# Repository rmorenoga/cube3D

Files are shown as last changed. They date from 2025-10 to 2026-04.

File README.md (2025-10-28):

https://github.com/user-attachments/assets/da8bfa61-0a1e-48aa-958f-0410e7f2b091

# Smart Cellular Bricks for Decentralized Shape Classification and Damage Recovery

## System Requirements
### Hardware requirements
Training, simulation and plot generation are setup as a Python jupyter notebook **BIGCUBE_V2.ipynb**. We reccomend Google [colab](https://colab.research.google.com/) to run it. To open the notebook in colab you can either clone this repository and upload the notebook to Google colab, or create a fork of the repository and open it directly from github using Google colab. Most cells run on the free version of colab, however, for training you should use one of the paid plans as it uses resources over the free limits (12 GB of RAM).

Firmware compilation and communication with the cubes has been tested on a standard computer running Windows 10 or 11. See **Cube Firmware** below. 

The electronics folder contains the electronic designs necessary to build a cube in order to run the classification code in the robots. 

### Software requirements
Follow the instructions in the jupyter notebook to install the required Python packages and run the different cells. The notebook runs on the 2025.07 runtime version of colab (see more information [here](https://research.google.com/colaboratory/runtime-version-faq.html#2025.07)). Other Python packages required include (See **Install all required python packages** inside the notebook):
- keras==2.11.0
- tensorflow==2.12.0
- pygifsicle

and the **gifsicle** program which can be installed by calling in a cell:

	!sudo apt-get install gifsicle

Uploading the firmware to the cubes uses Python scripts, the requirements.txt in /OTAPython/ lists the necessary dependencies.
Getting data from the cubes requires installing [docker](docker.com/) in your system.

Both functions have been tested in a standard computer with Windows 11. See further details in each section below.

# Installation instructions 

Training and simulation are performed using python code organized in a jupyter notebook that runs preferably in Google colab **BIGCUBE_V2.ipynb**. To open it you can either clone this repository and upload the notebook to Google colab, or create a fork of the repository and open it directly from github using Google colab. The notebook also contains functions for exporting the model weights as a file for compiling the microcontroller code, tools for checking connections between real cubes and tools for generating graphs. For further instructions check the different cell descriptions inside the notebook. 

## Outputting neural network for firmware
To output the neural network to be uploaded to the firmware, run the corresponding cell in the jupyter notebook. It produces a text file that can be copied directly into the neural_network.h required by the firmware.

## Cube firmware
The cube firmware is saved in the 3DCubePlatformIO folder. You also need the neural_network.h file located in the root file of the repository. The following steps have been tested on Windows 10 and 11.

### Compiling
To be able to upload the firmware to the cubes it should first be compiled. The 3DCubePlatformIO folder is set up and configured as a [platformIO](platformio.org/) project. To make things easier we reccomend opening the folder with [visual studio code](https://code.visualstudio.com/). VSCode will automatically detect the platformio.ini file in the repository and ask you to install the platformIO extension. The extension will then automatically donwload all the required compilers and libraries. After installation press the compile button (check mark at the bottom left corner of VSCode). This will generate the firmware.bin file in the 3DCubePlatformIO/.pio/build/adafruit_metro_esp32s2/ subfolder. 

### Uploading
To upload the firmware.bin file first make sure the cubes are connected to the same local network. Then navigate to the OTApython folder and run the ESPuploadParallel.py script. This script should upload the firmware to all cubes connected in the network. To change the subnet that is scanned by the script, change the address ranges in lines 18, 80, 86, 52 and 53.

### Getting data from the cubes

After all cubes have been programmed. Turn them off, navigate to the StateReceivers folder in a terminal and launch the following command:

	docker compose up

 This will run the server configured in **docker-compose.yaml**. This requires that you have [docker](docker.com/) installed in your system and assumes that you have a [mongodb](mongodb.com/) installation with a **Test** database and a **Dummy** collection set up. Additionally make sure that the computer where you launch the server is on IP 192.168.72.22 and that you have firewall permissions to receive on TCP port 8000. You can change the server address in the firmware (/3DCubePlatformIO/src/3d_cube.ino) in line 688, this needs the cubes to be reprogrammed. After you launch the server, turn on the assembled cubes. The cubes will first perform the classification process, then connect to the network specified in lines 602 and 603 in the firmware (/3DCubePlatformIO/src/3d_cube.ino) and then post the data to the server.

After the data from all cubes arrive to the server, you can export the collection as a .json file.

## Electronics
This folder contains the electronic PCB designs necessary to fabricate a cube.

## Training Data:

The training data is downloaded from https://www.shapenet.org/ as ModelShapeNetCore, model_normalized.solid.binvox format. We use 7 classes: aircraft, boat, car, guitar, birdhouse(house), table and chair.

This data is then reduced by the function “training_data_cleaning.py”. Running this file will present you with scaled down versions of the downloaded training data. If you think the image is acceptable, close the image popup, and write “y” into the terminal. Else, write “n” in the terminal. The terminal will display how many successful images have been saved and also the number of voxels in each piece of data. Note: the data is expected to be in the file subfolder location vox_data/…. Cleaning the data is done one class at a time, and labels are saved simultaneously with the xdata. To change the class type, change line 129. 

The classification output should be as follows:

**N.  Class   Color**
- 0 **Plane** green  
- 1 **Chair** blue  
- 2 **Car** purple  
- 3 **Table** yellow 
- 4 **House** white  
- 5 **Guitar** pink  
- 6 **Boat** cyan
- **Damaged** red

The code will output two .npy files xdata and ydata that are ready to be inputted to the neural network training code. **Already cleaned data is stored in the xdata_7class.npy and ydata_7class.npy**

## Training for damage detection and recovery

Our code for damage detection and recovery can be found here: https://github.com/shyamsn97/cube-regen

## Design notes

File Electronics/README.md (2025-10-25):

# Electronic PCB design files

This folder contains the design files for fabricating the PCBs that make the sides of the cube and that enable processing, power and communication. Each folder contains a [Kicad](kicad.org/) project with both schematics and layout files. 

## 3DESPWrover 
This is the top PCB that contains an ESP32-WROOVER module, a DC-DC step down converter and a Neo-pixel RGB led. The BoardTest subfolder contains test code to check that all components are working properly in the board. This PCB contains a 14-way micromatch connector to connect this and the bottom PCB together. One top PCB is required for one cube.

## 3DESPWroverS
This is the side PCB. This PCB contains only communication and power headers as well as soldering connections to attach it to other similar PCBs and the bottom one. Four identical side PCBs are required for one cube.

## 3DESPWroverB
This is the bottom PCB. This PCB contains only communication and power headers as well as soldering connections to attach it to the side PCBs. This PCB contains a 14-way micromatch connector to connect this and the top PCB together. One bottom PCB is required for one cube.

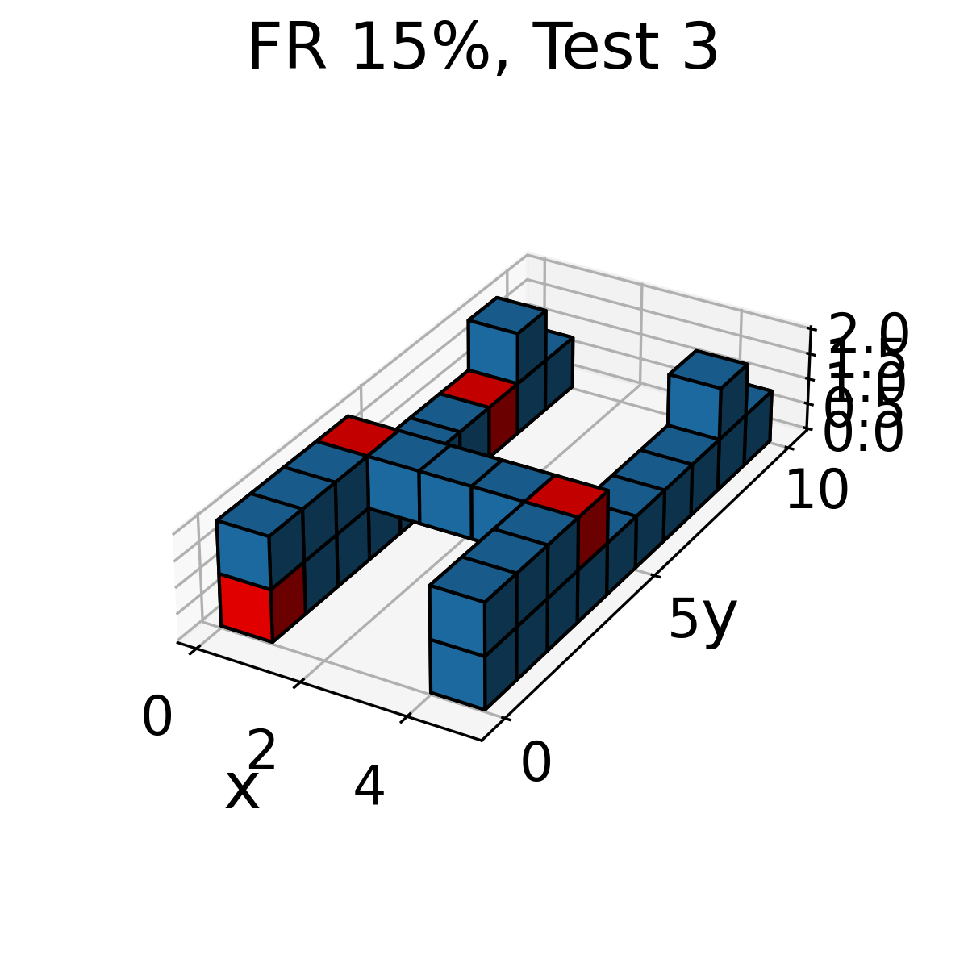
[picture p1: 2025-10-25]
Experiment data/hardware/Boat_144/Boat_144_FR15_T3.png

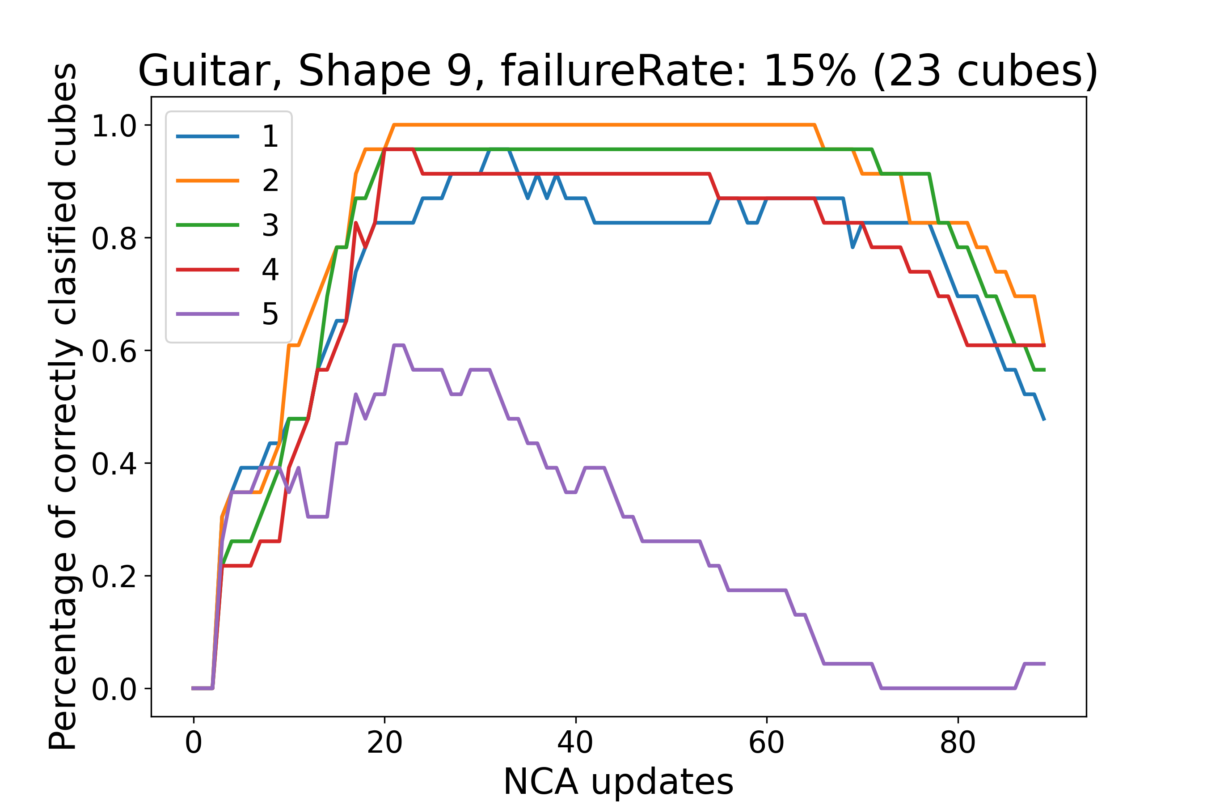
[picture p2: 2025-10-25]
Experiment data/hardware/Guitar_9/GraphGuitar_9_FR15.png

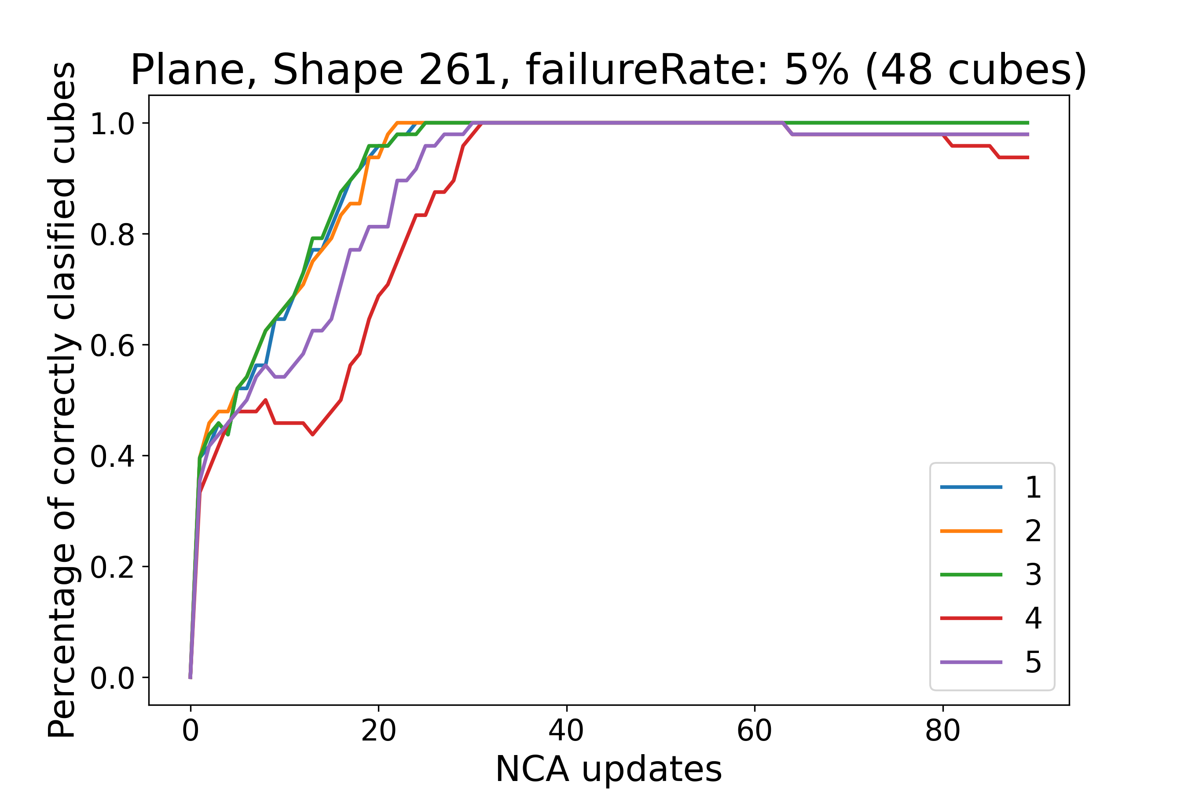
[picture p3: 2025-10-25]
Experiment data/hardware/Plane_261/GraphPlane_261_FR5.png

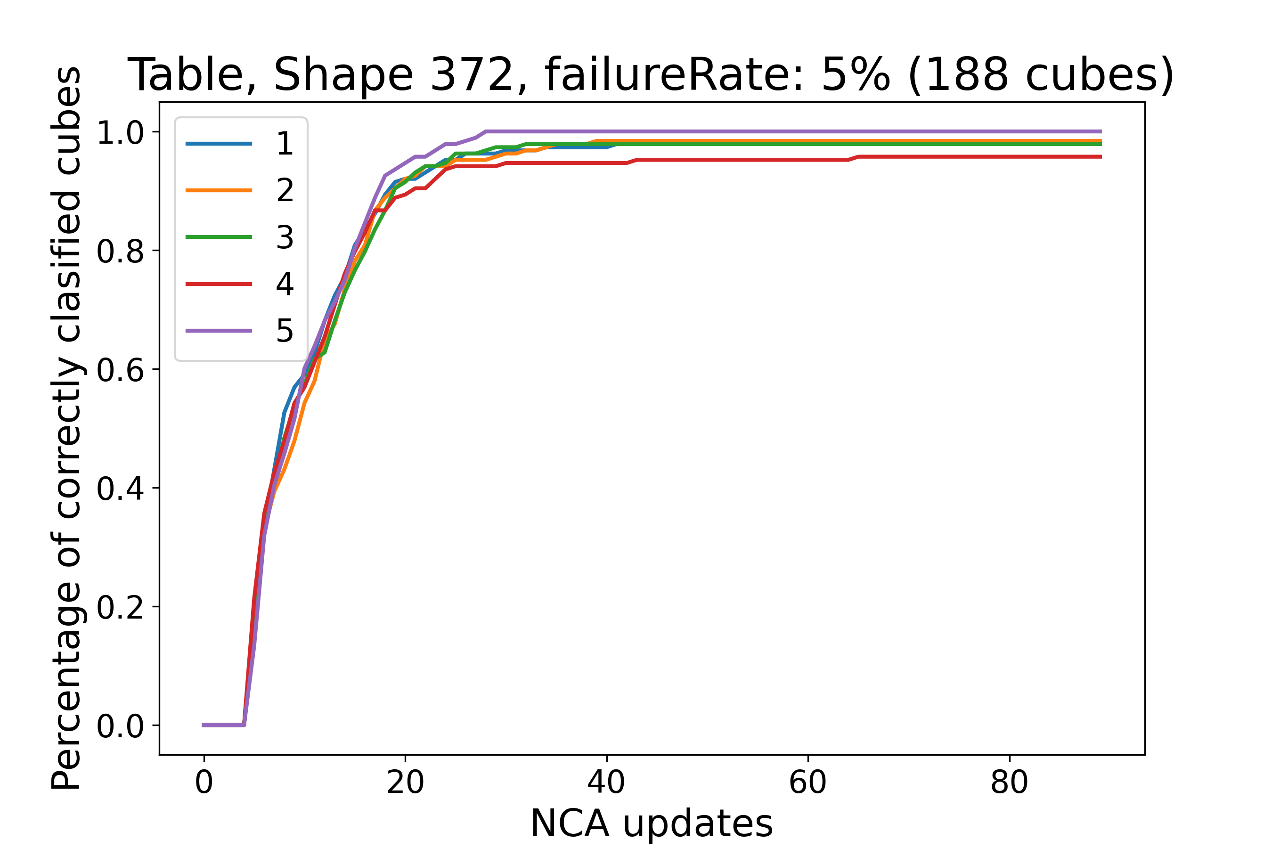
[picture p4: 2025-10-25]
Experiment data/hardware/Table_372/GraphTable_372_FR5.png

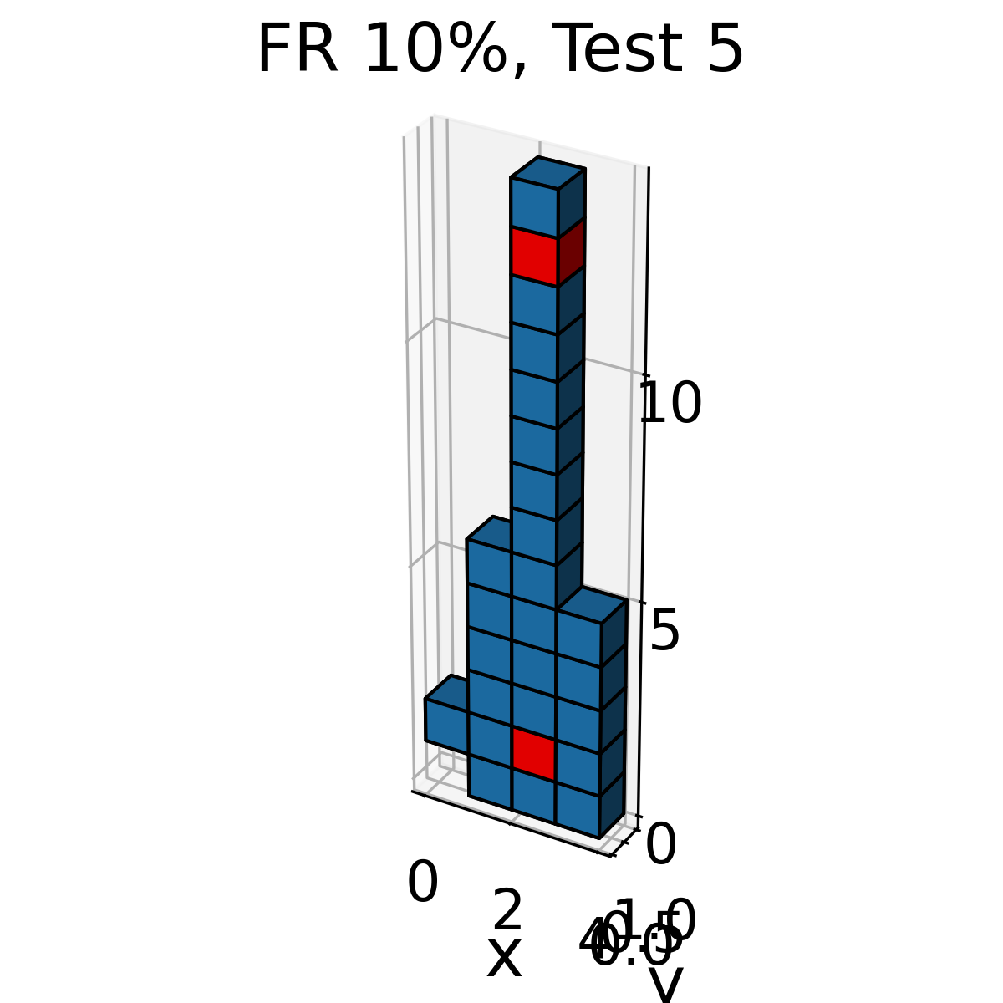
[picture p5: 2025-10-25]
Experiment data/hardware/Guitar_9/Guitar_9_FR10_T5.png

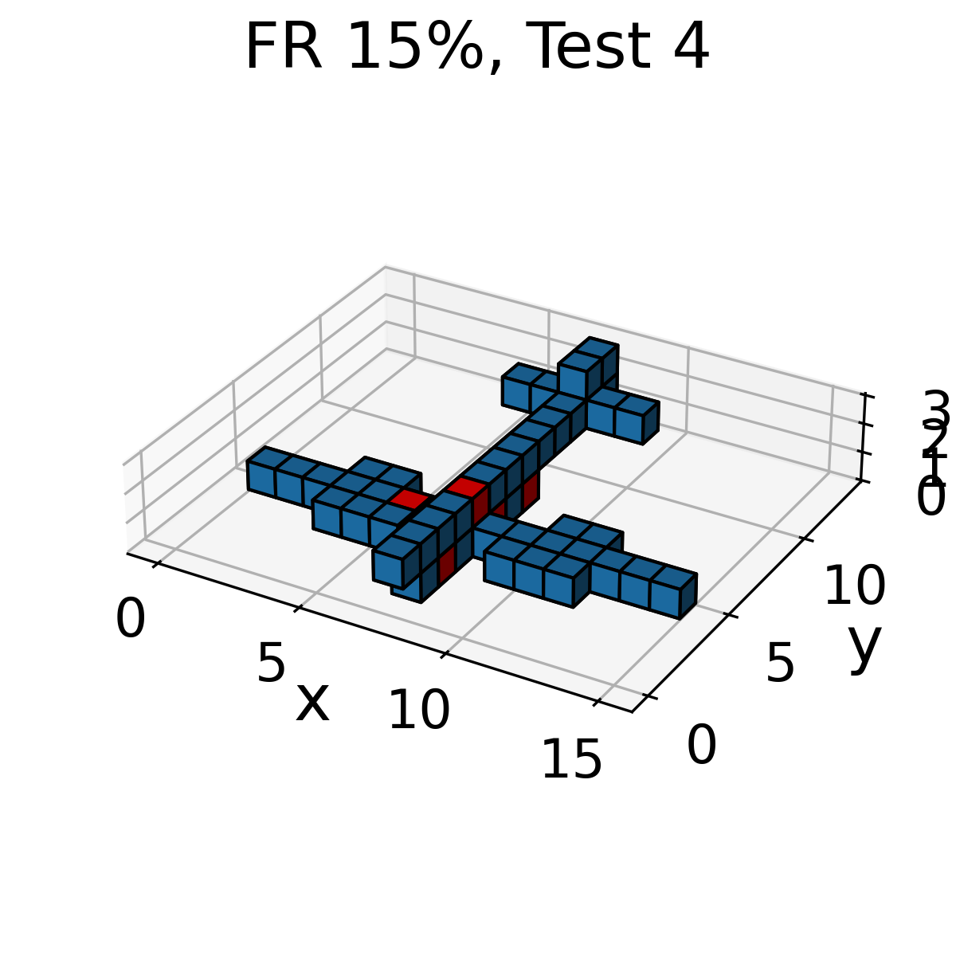
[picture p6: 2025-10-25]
Experiment data/hardware/Plane_261/Plane_261_FR15_T4.png

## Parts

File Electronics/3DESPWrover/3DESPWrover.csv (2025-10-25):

Reference, Value, Footprint, Datasheet, Voltage
U1,"ESP32-S2-WROVER","RF_Module:ESP32-S2-WROVER","https://www.espressif.com/sites/default/files/documentation/esp32-s2-wrover_esp32-s2-wrover-i_datasheet_en.pdf"
C1,"10u","Capacitor_SMD:C_0805_2012Metric_Pad1.18x1.45mm_HandSolder","~" | x
C2,"10u","Capacitor_SMD:C_0805_2012Metric_Pad1.18x1.45mm_HandSolder","~" | x
C3,"10u","Capacitor_SMD:C_0805_2012Metric_Pad1.18x1.45mm_HandSolder","~" | x
C4,"10u","Capacitor_SMD:C_0805_2012Metric_Pad1.18x1.45mm_HandSolder","~" | x
J2,"Conn_01x03_Female","Connector_PinHeader_2.54mm:PinHeader_1x03_P2.54mm_Vertical","~" | x
C9,"22u","Capacitor_SMD:C_0805_2012Metric_Pad1.18x1.45mm_HandSolder","~","10V" | x
C10,"22u","Capacitor_SMD:C_0805_2012Metric_Pad1.18x1.45mm_HandSolder","~","10V" | x
C11,"10u","Capacitor_SMD:C_0805_2012Metric_Pad1.18x1.45mm_HandSolder","~","50V" | x
L1,"10u","Custom:L_4.5x4_H3.2","~" | x
SW2,"SW_Push","Button_Switch_SMD:SW_SPST_B3S-1000","~" | x
SW1,"SW_Push","Button_Switch_SMD:SW_SPST_B3S-1000","~" | x
C8,"1u","Capacitor_SMD:C_0805_2012Metric_Pad1.18x1.45mm_HandSolder","~" | x
R3,"10k","Resistor_SMD:R_0805_2012Metric_Pad1.20x1.40mm_HandSolder","~" | x
D1,"WS2812B","LED_SMD:LED_WS2812B_PLCC4_5.0x5.0mm_P3.2mm","https://cdn-shop.adafruit.com/datasheets/WS2812B.pdf"
R1,"5.1k","Resistor_SMD:R_0805_2012Metric_Pad1.20x1.40mm_HandSolder","~" | x
R2,"5.1k","Resistor_SMD:R_0805_2012Metric_Pad1.20x1.40mm_HandSolder","~" | x
C6,"0.1u","Capacitor_SMD:C_0805_2012Metric_Pad1.18x1.45mm_HandSolder","~" | x
J1,"Conn_01x05_Male","Connector_PinHeader_2.54mm:PinHeader_1x05_P2.54mm_Vertical","~" | x
J3,"Conn_02x03_Odd_Even","Connector_PinHeader_2.54mm:PinHeader_2x03_P2.54mm_Vertical","~" | x
J4,"Conn_02x07_Odd_Even","Custom:TE_Micromatch_2,54_14","~" | x
R4,"10k","Resistor_SMD:R_0805_2012Metric_Pad1.20x1.40mm_HandSolder","~" | x
NT1,"Net-Tie_2","NetTie:NetTie-2_SMD_Pad0.5mm","~"

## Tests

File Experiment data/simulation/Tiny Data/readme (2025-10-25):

Data collected from first round of limitation testing.
Test shapes generated using zoom of 0.12

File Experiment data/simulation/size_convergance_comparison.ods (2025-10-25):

No. Cubes | Class | Time to convergence
219 | 3 | 60
277 | 3 | 41
161 | 3 | 60
424 | 3 | 46
245 | 3 | 31
208 | 3 | 46
378 | 3 | 41
147 | 3 | 36
144 | 3 | 36
261 | 3 | 46
186 | 1 | 43
234 | 1 | 29
194 | 1 | 43
294 | 1 | 36
1757 | 1 | 36
264 | 1 | 37
192 | 1 | 38
136 | 1 | 39
141 | 1 | 40
9 | 0 | 18
9 | 0 | 19
6 | 0 | 13
7 | 0 | 19
6 | 0 | 15
8 | 0 | 16
6 | 0 | 16
9 | 0 | 16
36 | 3 | 30
45 | 3 | 46
33 | 3 | 32
33 | 3 | 35
40 | 3 | 34
42 | 3 | 42
37 | 0 | 16
35 | 0 | 16
42 | 0 | 20
49 | 0 | 22
29 | 0 | 16

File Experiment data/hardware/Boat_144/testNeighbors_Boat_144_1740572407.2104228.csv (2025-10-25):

2025-02-26 13:20:29.190856 | 2025-02-26 13:20:30.048945 | 176613923055464 | 0x68 | 0x67 | 0x25 | 0x22 | 0xa1 | 0xa0 | 0x0 | 0x0 | 0x68 | 0x67 | 0x25 | 0x25 | 0x34 | 0x24 | 0x0 | 0x0 | 0x68 | 0x67 | 0x25 | 0x22 | 0xb0 | 0x5e | 0x0 | 0x0 | 0x0 | 0x0 | 0x0 | 0x0 | 0x0 | 0x0 | 0x0 | 0x0 | 0x0 | 0x0 | 0x0 | 0x0 | 0x0 | 0x0 | 0x0 | 0x0 | 0x0 | 0x0 | 0x0 | 0x0 | 0x0 | 0x0 | 0x0 | 0x0 | 0x0 | 0x0 | 0x0 | 0x0 | 0x0 | 0x0 | 0x0 | 0x0 | 0
2025-02-26 13:20:29.190856 | 2025-02-26 13:20:30.048945 | 104110580131688 | 0x68 | 0x67 | 0x25 | 0x22 | 0xb0 | 0x5e | 0x0 | 0x0 | 0x68 | 0x67 | 0x25 | 0x22 | 0xa1 | 0xa0 | 0x0 | 0x0 | 0x68 | 0x67 | 0x25 | 0x24 | 0x5c | 0xa8 | 0x0 | 0x0 | 0x0 | 0x0 | 0x0 | 0x0 | 0x0 | 0x0 | 0x0 | 0x0 | 0x0 | 0x0 | 0x0 | 0x0 | 0x0 | 0x0 | 0x0 | 0x0 | 0x0 | 0x0 | 0x0 | 0x0 | 0x0 | 0x0 | 0x0 | 0x0 | 0x0 | 0x0 | 0x0 | 0x0 | 0x0 | 0x0 | 0x0 | 0x0 | 0
2025-02-26 13:20:29.190856 | 2025-02-26 13:20:30.048945 | 251660261248856 | 0x58 | 0xcf | 0x79 | 0x38 | 0xe2 | 0xe4 | 0x0 | 0x0 | 0x68 | 0x67 | 0x25 | 0x24 | 0x5c | 0xa8 | 0x0 | 0x0 | 0x68 | 0x67 | 0x25 | 0x26 | 0x1 | 0xc8 | 0x0 | 0x0 | 0x0 | 0x0 | 0x0 | 0x0 | 0x0 | 0x0 | 0x0 | 0x0 | 0x0 | 0x0 | 0x0 | 0x0 | 0x0 | 0x0 | 0x0 | 0x0 | 0x0 | 0x0 | 0x0 | 0x0 | 0x0 | 0x0 | 0x0 | 0x0 | 0x0 | 0x0 | 0x0 | 0x0 | 0x0 | 0x0 | 0x0 | 0x0 | 0
2025-02-26 13:20:29.190856 | 2025-02-26 13:20:30.048945 | 176373471995752 | 0x68 | 0x67 | 0x25 | 0x26 | 0x69 | 0xa0 | 0x0 | 0x0 | 0x68 | 0x67 | 0x25 | 0x24 | 0xbb | 0x30 | 0x0 | 0x0 | 0x68 | 0x67 | 0x25 | 0x25 | 0xeb | 0x1c | 0x0 | 0x0 | 0x0 | 0x0 | 0x0 | 0x0 | 0x0 | 0x0 | 0x0 | 0x0 | 0x0 | 0x0 | 0x0 | 0x0 | 0x0 | 0x0 | 0x0 | 0x0 | 0x0 | 0x0 | 0x0 | 0x0 | 0x0 | 0x0 | 0x0 | 0x0 | 0x68 | 0x67 | 0x25 | 0x22 | 0xb8 | 0x10 | 0x0 | 0x0 | 0
2025-02-26 13:20:29.190856 | 2025-02-26 13:20:30.048945 | 42585173616488 | 0x68 | 0x67 | 0x25 | 0x22 | 0xbb | 0x26 | 0x0 | 0x0 | 0x68 | 0x67 | 0x25 | 0x26 | 0x1 | 0xc8 | 0x0 | 0x0 | 0x0 | 0x0 | 0x0 | 0x0 | 0x0 | 0x0 | 0x0 | 0x0 | 0x0 | 0x0 | 0x0 | 0x0 | 0x0 | 0x0 | 0x0 | 0x0 | 0x0 | 0x0 | 0x0 | 0x0 | 0x0 | 0x0 | 0x0 | 0x0 | 0x0 | 0x0 | 0x0 | 0x0 | 0x0 | 0x0 | 0x0 | 0x0 | 0x0 | 0x0 | 0x0 | 0x0 | 0x0 | 0x0 | 0x0 | 0x0 | 0
2025-02-26 13:20:29.190856 | 2025-02-26 13:20:30.048945 | 53580323448680 | 0x68 | 0x67 | 0x25 | 0x24 | 0xbb | 0x30 | 0x0 | 0x0 | 0x0 | 0x0 | 0x0 | 0x0 | 0x0 | 0x0 | 0x0 | 0x0 | 0x68 | 0x67 | 0x25 | 0x26 | 0x69 | 0xa0 | 0x0 | 0x0 | 0x0 | 0x0 | 0x0 | 0x0 | 0x0 | 0x0 | 0x0 | 0x0 | 0x0 | 0x0 | 0x0 | 0x0 | 0x0 | 0x0 | 0x0 | 0x0 | 0x0 | 0x0 | 0x0 | 0x0 | 0x0 | 0x0 | 0x0 | 0x0 | 0x60 | 0x55 | 0xf9 | 0xd9 | 0x2a | 0x6a | 0x0 | 0x0 | 0
2025-02-26 13:20:29.190856 | 2025-02-26 13:20:30.048945 | 80191957591912 | 0x68 | 0x67 | 0x25 | 0x25 | 0xef | 0x48 | 0x0 | 0x0 | 0x60 | 0x55 | 0xf9 | 0xe1 | 0xe5 | 0xfa | 0x0 | 0x0 | 0x68 | 0x67 | 0x25 | 0x26 | 0x0 | 0x30 | 0x0 | 0x0 | 0x0 | 0x0 | 0x0 | 0x0 | 0x0 | 0x0 | 0x0 | 0x0 | 0x0 | 0x0 | 0x0 | 0x0 | 0x0 | 0x0 | 0x0 | 0x0 | 0x0 | 0x0 | 0x0 | 0x0 | 0x0 | 0x0 | 0x0 | 0x0 | 0x68 | 0x67 | 0x25 | 0x24 | 0x8c | 0x2a | 0x0 | 0x0 | 0
2025-02-26 13:20:29.190856 | 2025-02-26 13:20:30.048945 | 52777198118760 | 0x68 | 0x67 | 0x25 | 0x26 | 0x0 | 0x30 | 0x0 | 0x0 | 0x68 | 0x67 | 0x25 | 0x25 | 0xef | 0x48 | 0x0 | 0x0 | 0x0 | 0x0 | 0x0 | 0x0 | 0x0 | 0x0 | 0x0 | 0x0 | 0x0 | 0x0 | 0x0 | 0x0 | 0x0 | 0x0 | 0x0 | 0x0 | 0x0 | 0x0 | 0x0 | 0x0 | 0x0 | 0x0 | 0x0 | 0x0 | 0x0 | 0x0 | 0x0 | 0x0 | 0x0 | 0x0 | 0x0 | 0x0 | 0x0 | 0x0 | 0x0 | 0x0 | 0x0 | 0x0 | 0x0 | 0x0 | 0
2025-02-26 13:20:29.190856 | 2025-02-26 13:20:30.048945 | 192290928316248 | 0x58 | 0xcf | 0x79 | 0x38 | 0xe3 | 0xae | 0x0 | 0x0 | 0x0 | 0x0 | 0x0 | 0x0 | 0x0 | 0x0 | 0x0 | 0x0 | 0x0 | 0x0 | 0x0 | 0x0 | 0x0 | 0x0 | 0x0 | 0x0 | 0x68 | 0x67 | 0x25 | 0x22 | 0xbb | 0x7e | 0x0 | 0x0 | 0x68 | 0x67 | 0x25 | 0x22 | 0xab | 0xe0 | 0x0 | 0x0 | 0x0 | 0x0 | 0x0 | 0x0 | 0x0 | 0x0 | 0x0 | 0x0 | 0x0 | 0x0 | 0x0 | 0x0 | 0x0 | 0x0 | 0x0 | 0x0 | 0
2025-02-26 13:20:29.190856 | 2025-02-26 13:20:30.048945 | 253635571574632 | 0x68 | 0x67 | 0x25 | 0x22 | 0xae | 0xe6 | 0x0 | 0x0 | 0x68 | 0x67 | 0x25 | 0x24 | 0xbc | 0xd6 | 0x0 | 0x0 | 0x60 | 0x55 | 0xf9 | 0xe1 | 0xe5 | 0xfa | 0x0 | 0x0 | 0x0 | 0x0 | 0x0 | 0x0 | 0x0 | 0x0 | 0x0 | 0x0 | 0x0 | 0x0 | 0x0 | 0x0 | 0x0 | 0x0 | 0x0 | 0x0 | 0x0 | 0x0 | 0x0 | 0x0 | 0x0 | 0x0 | 0x0 | 0x0 | 0x0 | 0x0 | 0x0 | 0x0 | 0x0 | 0x0 | 0x0 | 0x0 | 0
2025-02-26 13:20:29.190856 | 2025-02-26 13:20:30.048945 | 247025616906088 | 0x68 | 0x67 | 0x25 | 0x22 | 0xab | 0xe0 | 0x0 | 0x0 | 0x0 | 0x0 | 0x0 | 0x0 | 0x0 | 0x0 | 0x0 | 0x0 | 0x0 | 0x0 | 0x0 | 0x0 | 0x0 | 0x0 | 0x0 | 0x0 | 0x58 | 0xcf | 0x79 | 0x38 | 0xe3 | 0xae | 0x0 | 0x0 | 0x68 | 0x67 | 0x25 | 0x25 | 0xfd | 0x54 | 0x0 | 0x0 | 0x0 | 0x0 | 0x0 | 0x0 | 0x0 | 0x0 | 0x0 | 0x0 | 0x0 | 0x0 | 0x0 | 0x0 | 0x0 | 0x0 | 0x0 | 0x0 | 0
2025-02-26 13:20:29.190856 | 2025-02-26 13:20:30.048945 | 139634304968552 | 0x68 | 0x67 | 0x25 | 0x25 | 0xff | 0x7e | 0x0 | 0x0 | 0x68 | 0x67 | 0x25 | 0x25 | 0xe7 | 0x28 | 0x0 | 0x0 | 0x0 | 0x0 | 0x0 | 0x0 | 0x0 | 0x0 | 0x0 | 0x0 | 0x0 | 0x0 | 0x0 | 0x0 | 0x0 | 0x0 | 0x0 | 0x0 | 0x68 | 0x67 | 0x25 | 0x22 | 0xbb | 0x7e | 0x0 | 0x0 | 0x68 | 0x67 | 0x25 | 0x25 | 0x34 | 0x24 | 0x0 | 0x0 | 0x0 | 0x0 | 0x0 | 0x0 | 0x0 | 0x0 | 0x0 | 0x0 | 0
2025-02-26 13:20:29.190856 | 2025-02-26 13:20:30.048945 | 93446226667368 | 0x68 | 0x67 | 0x25 | 0x25 | 0xfd | 0x54 | 0x0 | 0x0 | 0x60 | 0x55 | 0xf9 | 0xda | 0x92 | 0x8c | 0x0 | 0x0 | 0x0 | 0x0 | 0x0 | 0x0 | 0x0 | 0x0 | 0x0 | 0x0 | 0x68 | 0x67 | 0x25 | 0x22 | 0xab | 0xe0 | 0x0 | 0x0 | 0x0 | 0x0 | 0x0 | 0x0 | 0x0 | 0x0 | 0x0 | 0x0 | 0x60 | 0x55 | 0xf9 | 0xd9 | 0xe1 | 0xe2 | 0x0 | 0x0 | 0x0 | 0x0 | 0x0 | 0x0 | 0x0 | 0x0 | 0x0 | 0x0 | 0
2025-02-26 13:20:29.190856 | 2025-02-26 13:20:30.048945 | 249459652515168 | 0x60 | 0x55 | 0xf9 | 0xd9 | 0xe1 | 0xe2 | 0x0 | 0x0 | 0x68 | 0x67 | 0x25 | 0x26 | 0x3 | 0x72 | 0x0 | 0x0 | 0x68 | 0x67 | 0x25 | 0x24 | 0x8f | 0xd0 | 0x0 | 0x0 | 0x0 | 0x0 | 0x0 | 0x0 | 0x0 | 0x0 | 0x0 | 0x0 | 0x0 | 0x0 | 0x0 | 0x0 | 0x0 | 0x0 | 0x0 | 0x0 | 0x0 | 0x0 | 0x0 | 0x0 | 0x0 | 0x0 | 0x0 | 0x0 | 0x68 | 0x67 | 0x25 | 0x25 | 0xfd | 0x54 | 0x0 | 0x0 | 0
2025-02-26 13:20:29.190856 | 2025-02-26 13:20:30.048945 | 39806380107624 | 0x68 | 0x67 | 0x25 | 0x25 | 0x34 | 0x24 | 0x0 | 0x0 | 0x68 | 0x67 | 0x25 | 0x25 | 0xeb | 0x1c | 0x0 | 0x0 | 0x68 | 0x67 | 0x25 | 0x22 | 0xa1 | 0xa0 | 0x0 | 0x0 | 0x0 | 0x0 | 0x0 | 0x0 | 0x0 | 0x0 | 0x0 | 0x0 | 0x0 | 0x0 | 0x0 | 0x0 | 0x0 | 0x0 | 0x0 | 0x0 | 0x0 | 0x0 | 0x0 | 0x0 | 0x0 | 0x0 | 0x0 | 0x0 | 0x68 | 0x67 | 0x25 | 0x25 | 0xff | 0x7e | 0x0 | 0x0 | 0
2025-02-26 13:20:29.190856 | 2025-02-26 13:20:30.048945 | 44973225764712 | 0x68 | 0x67 | 0x25 | 0x25 | 0xe7 | 0x28 | 0x0 | 0x0 | 0x68 | 0x67 | 0x25 | 0x22 | 0xb8 | 0x10 | 0x0 | 0x0 | 0x68 | 0x67 | 0x25 | 0x25 | 0xff | 0x7e | 0x0 | 0x0 | 0x0 | 0x0 | 0x0 | 0x0 | 0x0 | 0x0 | 0x0 | 0x0 | 0x0 | 0x0 | 0x0 | 0x0 | 0x0 | 0x0 | 0x0 | 0x0 | 0x68 | 0x67 | 0x25 | 0x25 | 0xeb | 0x1c | 0x0 | 0x0 | 0x0 | 0x0 | 0x0 | 0x0 | 0x0 | 0x0 | 0x0 | 0x0 | 0
2025-02-26 13:20:29.190856 | 2025-02-26 13:20:30.048945 | 139342196860776 | 0x68 | 0x67 | 0x25 | 0x22 | 0xbb | 0x7e | 0x0 | 0x0 | 0x0 | 0x0 | 0x0 | 0x0 | 0x0 | 0x0 | 0x0 | 0x0 | 0x0 | 0x0 | 0x0 | 0x0 | 0x0 | 0x0 | 0x0 | 0x0 | 0x68 | 0x67 | 0x25 | 0x25 | 0xff | 0x7e | 0x0 | 0x0 | 0x58 | 0xcf | 0x79 | 0x38 | 0xe3 | 0xae | 0x0 | 0x0 | 0x0 | 0x0 | 0x0 | 0x0 | 0x0 | 0x0 | 0x0 | 0x0 | 0x0 | 0x0 | 0x0 | 0x0 | 0x0 | 0x0 | 0x0 | 0x0 | 0
2025-02-26 13:20:29.190856 | 2025-02-26 13:20:30.048945 | 229313205331816 | 0x68 | 0x67 | 0x25 | 0x24 | 0x8f | 0xd0 | 0x0 | 0x0 | 0x60 | 0x55 | 0xf9 | 0xd9 | 0xe1 | 0xe2 | 0x0 | 0x0 | 0x68 | 0x67 | 0x25 | 0x24 | 0xbc | 0xd6 | 0x0 | 0x0 | 0x0 | 0x0 | 0x0 | 0x0 | 0x0 | 0x0 | 0x0 | 0x0 | 0x0 | 0x0 | 0x0 | 0x0 | 0x0 | 0x0 | 0x0 | 0x0 | 0x0 | 0x0 | 0x0 | 0x0 | 0x0 | 0x0 | 0x0 | 0x0 | 0x0 | 0x0 | 0x0 | 0x0 | 0x0 | 0x0 | 0x0 | 0x0 | 0
2025-02-26 13:20:29.190856 | 2025-02-26 13:20:30.048945 | 18383032903528 | 0x68 | 0x67 | 0x25 | 0x22 | 0xb8 | 0x10 | 0x0 | 0x0 | 0x60 | 0x55 | 0xf9 | 0xd9 | 0x2a | 0x6a | 0x0 | 0x0 | 0x68 | 0x67 | 0x25 | 0x25 | 0xe7 | 0x28 | 0x0 | 0x0 | 0x0 | 0x0 | 0x0 | 0x0 | 0x0 | 0x0 | 0x0 | 0x0 | 0x0 | 0x0 | 0x0 | 0x0 | 0x0 | 0x0 | 0x0 | 0x0 | 0x68 | 0x67 | 0x25 | 0x26 | 0x69 | 0xa0 | 0x0 | 0x0 | 0x0 | 0x0 | 0x0 | 0x0 | 0x0 | 0x0 | 0x0 | 0x0 | 0
2025-02-26 13:20:29.190856 | 2025-02-26 13:20:30.048945 | 31796266100584 | 0x68 | 0x67 | 0x25 | 0x25 | 0xeb | 0x1c | 0x0 | 0x0 | 0x68 | 0x67 | 0x25 | 0x26 | 0x69 | 0xa0 | 0x0 | 0x0 | 0x68 | 0x67 | 0x25 | 0x25 | 0x34 | 0x24 | 0x0 | 0x0 | 0x0 | 0x0 | 0x0 | 0x0 | 0x0 | 0x0 | 0x0 | 0x0 | 0x0 | 0x0 | 0x0 | 0x0 | 0x0 | 0x0 | 0x0 | 0x0 | 0x0 | 0x0 | 0x0 | 0x0 | 0x0 | 0x0 | 0x0 | 0x0 | 0x68 | 0x67 | 0x25 | 0x25 | 0xe7 | 0x28 | 0x0 | 0x0 | 0
2025-02-26 13:20:29.190856 | 2025-02-26 13:20:30.048945 | 125357850453864 | 0x68 | 0x67 | 0x25 | 0x26 | 0x3 | 0x72 | 0x0 | 0x0 | 0x68 | 0x67 | 0x25 | 0x25 | 0xf2 | 0x82 | 0x0 | 0x0 | 0x60 | 0x55 | 0xf9 | 0xd9 | 0xe1 | 0xe2 | 0x0 | 0x0 | 0x0 | 0x0 | 0x0 | 0x0 | 0x0 | 0x0 | 0x0 | 0x0 | 0x0 | 0x0 | 0x0 | 0x0 | 0x0 | 0x0 | 0x0 | 0x0 | 0x0 | 0x0 | 0x0 | 0x0 | 0x0 | 0x0 | 0x0 | 0x0 | 0x60 | 0x55 | 0xf9 | 0xda | 0x92 | 0x8c | 0x0 | 0x0 | 0
2025-02-26 13:20:29.190856 | 2025-02-26 13:20:30.048945 | 154562366887264 | 0x60 | 0x55 | 0xf9 | 0xda | 0x92 | 0x8c | 0x0 | 0x0 | 0x68 | 0x67 | 0x25 | 0x25 | 0x84 | 0xb0 | 0x0 | 0x0 | 0x68 | 0x67 | 0x25 | 0x25 | 0xfd | 0x54 | 0x0 | 0x0 | 0x0 | 0x0 | 0x0 | 0x0 | 0x0 | 0x0 | 0x0 | 0x0 | 0x0 | 0x0 | 0x0 | 0x0 | 0x0 | 0x0 | 0x0 | 0x0 | 0x68 | 0x67 | 0x25 | 0x26 | 0x3 | 0x72 | 0x0 | 0x0 | 0x0 | 0x0 | 0x0 | 0x0 | 0x0 | 0x0 | 0x0 | 0x0 | 0
2025-02-26 13:20:29.190856 | 2025-02-26 13:20:30.048945 | 46781390219112 | 0x68 | 0x67 | 0x25 | 0x24 | 0x8c | 0x2a | 0x0 | 0x0 | 0x0 | 0x0 | 0x0 | 0x0 | 0x0 | 0x0 | 0x0 | 0x0 | 0x0 | 0x0 | 0x0 | 0x0 | 0x0 | 0x0 | 0x0 | 0x0 | 0x0 | 0x0 | 0x0 | 0x0 | 0x0 | 0x0 | 0x0 | 0x0 | 0x0 | 0x0 | 0x0 | 0x0 | 0x0 | 0x0 | 0x0 | 0x0 | 0x68 | 0x67 | 0x25 | 0x25 | 0xef | 0x48 | 0x0 | 0x0 | 0x0 | 0x0 | 0x0 | 0x0 | 0x0 | 0x0 | 0x0 | 0x0 | 0
2025-02-26 13:20:29.190856 | 2025-02-26 13:20:30.048945 | 185113696888680 | 0x68 | 0x67 | 0x25 | 0x24 | 0x5c | 0xa8 | 0x0 | 0x0 | 0x68 | 0x67 | 0x25 | 0x22 | 0xb0 | 0x5e | 0x0 | 0x0 | 0x58 | 0xcf | 0x79 | 0x38 | 0xe2 | 0xe4 | 0x0 | 0x0 | 0x0 | 0x0 | 0x0 | 0x0 | 0x0 | 0x0 | 0x0 | 0x0 | 0x0 | 0x0 | 0x0 | 0x0 | 0x0 | 0x0 | 0x0 | 0x0 | 0x0 | 0x0 | 0x0 | 0x0 | 0x0 | 0x0 | 0x0 | 0x0 | 0x0 | 0x0 | 0x0 | 0x0 | 0x0 | 0x0 | 0x0 | 0x0 | 0
2025-02-26 13:20:29.190856 | 2025-02-26 13:20:30.048945 | 236103548626792 | 0x68 | 0x67 | 0x25 | 0x24 | 0xbc | 0xd6 | 0x0 | 0x0 | 0x68 | 0x67 | 0x25 | 0x24 | 0x8f | 0xd0 | 0x0 | 0x0 | 0x68 | 0x67 | 0x25 | 0x22 | 0xae | 0xe6 | 0x0 | 0x0 | 0x0 | 0x0 | 0x0 | 0x0 | 0x0 | 0x0 | 0x0 | 0x0 | 0x0 | 0x0 | 0x0 | 0x0 | 0x0 | 0x0 | 0x0 | 0x0 | 0x0 | 0x0 | 0x0 | 0x0 | 0x0 | 0x0 | 0x0 | 0x0 | 0x0 | 0x0 | 0x0 | 0x0 | 0x0 | 0x0 | 0x0 | 0x0 | 0
2025-02-26 13:20:29.190856 | 2025-02-26 13:20:30.048945 | 143976516904808 | 0x68 | 0x67 | 0x25 | 0x25 | 0xf2 | 0x82 | 0x0 | 0x0 | 0x68 | 0x67 | 0x25 | 0x25 | 0xf0 | 0xf0 | 0x0 | 0x0 | 0x68 | 0x67 | 0x25 | 0x26 | 0x3 | 0x72 | 0x0 | 0x0 | 0x0 | 0x0 | 0x0 | 0x0 | 0x0 | 0x0 | 0x0 | 0x0 | 0x0 | 0x0 | 0x0 | 0x0 | 0x0 | 0x0 | 0x0 | 0x0 | 0x0 | 0x0 | 0x0 | 0x0 | 0x0 | 0x0 | 0x0 | 0x0 | 0x68 | 0x67 | 0x25 | 0x25 | 0x84 | 0xb0 | 0x0 | 0x0 | 0
2025-02-26 13:20:29.190856 | 2025-02-26 13:20:30.048945 | 275865245668704 | 0x60 | 0x55 | 0xf9 | 0xe1 | 0xe5 | 0xfa | 0x0 | 0x0 | 0x68 | 0x67 | 0x25 | 0x22 | 0xae | 0xe6 | 0x0 | 0x0 | 0x68 | 0x67 | 0x25 | 0x25 | 0xef | 0x48 | 0x0 | 0x0 | 0x0 | 0x0 | 0x0 | 0x0 | 0x0 | 0x0 | 0x0 | 0x0 | 0x0 | 0x0 | 0x0 | 0x0 | 0x0 | 0x0 | 0x0 | 0x0 | 0x0 | 0x0 | 0x0 | 0x0 | 0x0 | 0x0 | 0x0 | 0x0 | 0x0 | 0x0 | 0x0 | 0x0 | 0x0 | 0x0 | 0x0 | 0x0 | 0
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

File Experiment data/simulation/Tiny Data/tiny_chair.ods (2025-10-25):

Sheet: tiny_chair_1
0 | 0 | 0 | 0 | 0 | 0 | 0 | 0 | 0 | 0 | 0 | 0 | 0 | 0 | 0 | 0 | 0 | 0 | 0 | 0 | 0 | 0 | 0 | 0 | 0 | 0 | 0 | 0
0 | 3 | 0 | 0 | 0 | 3 | 0 | 3 | 0 | 0 | 0 | 3 | 3 | 3 | 0 | 0 | 0 | 3 | 0 | 0 | 0 | 1 | 3 | 3 | 0 | 0 | 1 | 3.84615384615385
0 | 3 | 0 | 0 | 0 | 3 | 1 | 3 | 0 | 0 | 3 | 3 | 3 | 1 | 3 | 3 | 3 | 3 | 0 | 0 | 0 | 1 | 3 | 3 | 3 | 0 | 3 | 11.5384615384615
0 | 3 | 0 | 0 | 0 | 3 | 1 | 3 | 0 | 0 | 3 | 3 | 3 | 1 | 3 | 3 | 3 | 3 | 0 | 0 | 0 | 1 | 3 | 1 | 3 | 0 | 4 | 15.3846153846154
0 | 3 | 0 | 0 | 0 | 3 | 1 | 3 | 1 | 0 | 3 | 3 | 3 | 1 | 3 | 3 | 3 | 3 | 0 | 0 | 0 | 1 | 1 | 1 | 3 | 0 | 6 | 23.0769230769231
0 | 3 | 0 | 0 | 3 | 3 | 1 | 1 | 1 | 0 | 3 | 3 | 1 | 1 | 3 | 3 | 3 | 3 | 0 | 0 | 3 | 1 | 1 | 1 | 1 | 0 | 9 | 34.6153846153846
3 | 3 | 0 | 0 | 3 | 1 | 1 | 1 | 1 | 0 | 3 | 3 | 1 | 1 | 3 | 3 | 3 | 3 | 0 | 0 | 3 | 1 | 1 | 1 | 1 | 0 | 10 | 38.4615384615385
3 | 3 | 0 | 0 | 3 | 1 | 1 | 1 | 1 | 0 | 3 | 3 | 1 | 1 | 3 | 3 | 3 | 3 | 0 | 0 | 1 | 1 | 1 | 1 | 1 | 0 | 11 | 42.3076923076923
3 | 3 | 0 | 3 | 1 | 1 | 1 | 1 | 1 | 0 | 3 | 3 | 1 | 1 | 1 | 3 | 3 | 3 | 0 | 0 | 1 | 1 | 1 | 1 | 1 | 0 | 13 | 50
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

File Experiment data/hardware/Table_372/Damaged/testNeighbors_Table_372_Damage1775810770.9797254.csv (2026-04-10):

2026-04-10 10:46:32.531890 | 2026-04-10 10:46:35.858837 | 170347616102248 | 0x68 | 0x67 | 0x25 | 0x25 | 0xee | 0x9a | 0x0 | 0x0 | 0x0 | 0x0 | 0x0 | 0x0 | 0x0 | 0x0 | 0x0 | 0x0 | 0x0 | 0x0 | 0x0 | 0x0 | 0x0 | 0x0 | 0x0 | 0x0 | 0x0 | 0x0 | 0x0 | 0x0 | 0x0 | 0x0 | 0x0 | 0x0 | 0x0 | 0x0 | 0x0 | 0x0 | 0x0 | 0x0 | 0x0 | 0x0 | 0x68 | 0x67 | 0x25 | 0x22 | 0xb6 | 0x4a | 0x0 | 0x0 | 0x60 | 0x55 | 0xf9 | 0xd9 | 0x2e | 0x90 | 0x0 | 0x0 | 0
2026-04-10 10:46:32.531890 | 2026-04-10 10:46:35.858837 | 18112466741096 | 0x68 | 0x67 | 0x25 | 0x23 | 0x79 | 0x10 | 0x0 | 0x0 | 0x60 | 0x55 | 0xf9 | 0xda | 0x92 | 0xb4 | 0x0 | 0x0 | 0x68 | 0x67 | 0x25 | 0x26 | 0xa1 | 0x18 | 0x0 | 0x0 | 0x68 | 0x67 | 0x25 | 0x26 | 0x1 | 0x7a | 0x0 | 0x0 | 0x68 | 0x67 | 0x25 | 0x23 | 0x1 | 0x2e | 0x0 | 0x0 | 0x0 | 0x0 | 0x0 | 0x0 | 0x0 | 0x0 | 0x0 | 0x0 | 0x0 | 0x0 | 0x0 | 0x0 | 0x0 | 0x0 | 0x0 | 0x0 | 0
2026-04-10 10:46:32.531890 | 2026-04-10 10:46:35.858837 | 88144975844704 | 0x60 | 0x55 | 0xf9 | 0xd9 | 0x2a | 0x50 | 0x0 | 0x0 | 0x68 | 0x67 | 0x25 | 0x22 | 0xf1 | 0xe4 | 0x0 | 0x0 | 0x58 | 0xcf | 0x79 | 0x38 | 0xe0 | 0x40 | 0x0 | 0x0 | 0x0 | 0x0 | 0x0 | 0x0 | 0x0 | 0x0 | 0x0 | 0x0 | 0x60 | 0x55 | 0xf9 | 0xe1 | 0xe5 | 0xca | 0x0 | 0x0 | 0x0 | 0x0 | 0x0 | 0x0 | 0x0 | 0x0 | 0x0 | 0x0 | 0x0 | 0x0 | 0x0 | 0x0 | 0x0 | 0x0 | 0x0 | 0x0 | 0
2026-04-10 10:46:32.531890 | 2026-04-10 10:46:35.858837 | 218662027513688 | 0x58 | 0xcf | 0x79 | 0x38 | 0xdf | 0xc6 | 0x0 | 0x0 | 0x68 | 0x67 | 0x25 | 0x22 | 0xf5 | 0x8c | 0x0 | 0x0 | 0x68 | 0x67 | 0x25 | 0x23 | 0x76 | 0x86 | 0x0 | 0x0 | 0x60 | 0x55 | 0xf9 | 0xd9 | 0x2e | 0x90 | 0x0 | 0x0 | 0x68 | 0x67 | 0x25 | 0x24 | 0xda | 0xa6 | 0x0 | 0x0 | 0x0 | 0x0 | 0x0 | 0x0 | 0x0 | 0x0 | 0x0 | 0x0 | 0x0 | 0x0 | 0x0 | 0x0 | 0x0 | 0x0 | 0x0 | 0x0 | 0
2026-04-10 10:46:32.531890 | 2026-04-10 10:46:35.858837 | 88678762637160 | 0x68 | 0x67 | 0x25 | 0x22 | 0xa7 | 0x50 | 0x0 | 0x0 | 0x0 | 0x0 | 0x0 | 0x0 | 0x0 | 0x0 | 0x0 | 0x0 | 0x60 | 0x55 | 0xf9 | 0xd9 | 0x2e | 0x90 | 0x0 | 0x0 | 0x0 | 0x0 | 0x0 | 0x0 | 0x0 | 0x0 | 0x0 | 0x0 | 0x68 | 0x67 | 0x25 | 0x22 | 0xf5 | 0x8c | 0x0 | 0x0 | 0x0 | 0x0 | 0x0 | 0x0 | 0x0 | 0x0 | 0x0 | 0x0 | 0x0 | 0x0 | 0x0 | 0x0 | 0x0 | 0x0 | 0x0 | 0x0 | 0
2026-04-10 10:46:32.531890 | 2026-04-10 10:46:35.858837 | 57371535168864 | 0x60 | 0x55 | 0xf9 | 0xd9 | 0x2d | 0x34 | 0x0 | 0x0 | 0x60 | 0x55 | 0xf9 | 0xd9 | 0x2d | 0x44 | 0x0 | 0x0 | 0x68 | 0x67 | 0x25 | 0x26 | 0x7f | 0x98 | 0x0 | 0x0 | 0x68 | 0x67 | 0x25 | 0x23 | 0x77 | 0xfa | 0x0 | 0x0 | 0x68 | 0x67 | 0x25 | 0x25 | 0xe7 | 0x8a | 0x0 | 0x0 | 0x0 | 0x0 | 0x0 | 0x0 | 0x0 | 0x0 | 0x0 | 0x0 | 0x0 | 0x0 | 0x0 | 0x0 | 0x0 | 0x0 | 0x0 | 0x0 | 0
2026-04-10 10:46:32.531890 | 2026-04-10 10:46:35.858837 | 27342709313368 | 0x58 | 0xcf | 0x79 | 0x38 | 0xde | 0x18 | 0x0 | 0x0 | 0x68 | 0x67 | 0x25 | 0x25 | 0xf6 | 0x1c | 0x0 | 0x0 | 0x68 | 0x67 | 0x25 | 0x23 | 0x1 | 0x2e | 0x0 | 0x0 | 0x60 | 0x55 | 0xf9 | 0xda | 0x92 | 0xb4 | 0x0 | 0x0 | 0x68 | 0x67 | 0x25 | 0x25 | 0xf1 | 0xd2 | 0x0 | 0x0 | 0x0 | 0x0 | 0x0 | 0x0 | 0x0 | 0x0 | 0x0 | 0x0 | 0x0 | 0x0 | 0x0 | 0x0 | 0x0 | 0x0 | 0x0 | 0x0 | 0
2026-04-10 10:46:32.531890 | 2026-04-10 10:46:35.858837 | 257956308674408 | 0x68 | 0x67 | 0x25 | 0x22 | 0x9c | 0xea | 0x0 | 0x0 | 0x60 | 0x55 | 0xf9 | 0xda | 0x92 | 0x58 | 0x0 | 0x0 | 0x68 | 0x67 | 0x25 | 0x25 | 0x1 | 0xc2 | 0x0 | 0x0 | 0x60 | 0x55 | 0xf9 | 0xe1 | 0xe6 | 0x12 | 0x0 | 0x0 | 0x0 | 0x0 | 0x0 | 0x0 | 0x0 | 0x0 | 0x0 | 0x0 | 0x0 | 0x0 | 0x0 | 0x0 | 0x0 | 0x0 | 0x0 | 0x0 | 0x0 | 0x0 | 0x0 | 0x0 | 0x0 | 0x0 | 0x0 | 0x0 | 0
2026-04-10 10:46:32.531890 | 2026-04-10 10:46:35.858837 | 53082107242344 | 0x68 | 0x67 | 0x25 | 0x24 | 0x47 | 0x30 | 0x0 | 0x0 | 0x0 | 0x0 | 0x0 | 0x0 | 0x0 | 0x0 | 0x0 | 0x0 | 0x68 | 0x67 | 0x25 | 0x22 | 0x9e | 0x30 | 0x0 | 0x0 | 0x60 | 0x55 | 0xf9 | 0xd9 | 0x2a | 0x88 | 0x0 | 0x0 | 0x68 | 0x67 | 0x25 | 0x22 | 0xb7 | 0x96 | 0x0 | 0x0 | 0x0 | 0x0 | 0x0 | 0x0 | 0x0 | 0x0 | 0x0 | 0x0 | 0x0 | 0x0 | 0x0 | 0x0 | 0x0 | 0x0 | 0x0 | 0x0 | 0
2026-04-10 10:46:32.531890 | 2026-04-10 10:46:35.858837 | 9780263741288 | 0x68 | 0x67 | 0x25 | 0x25 | 0xe5 | 0x8 | 0x0 | 0x0 | 0x68 | 0x67 | 0x25 | 0x26 | 0x6 | 0x86 | 0x0 | 0x0 | 0x68 | 0x67 | 0x25 | 0x22 | 0xab | 0xb0 | 0x0 | 0x0 | 0x68 | 0x67 | 0x25 | 0x22 | 0xb7 | 0x70 | 0x0 | 0x0 | 0x60 | 0x55 | 0xf9 | 0xe1 | 0xe6 | 0x12 | 0x0 | 0x0 | 0x0 | 0x0 | 0x0 | 0x0 | 0x0 | 0x0 | 0x0 | 0x0 | 0x0 | 0x0 | 0x0 | 0x0 | 0x0 | 0x0 | 0x0 | 0x0 | 0
2026-04-10 10:46:32.531890 | 2026-04-10 10:46:35.858837 | 117291834763112 | 0x68 | 0x67 | 0x25 | 0x22 | 0xad | 0x6a | 0x0 | 0x0 | 0x68 | 0x67 | 0x25 | 0x22 | 0xa1 | 0x58 | 0x0 | 0x0 | 0x68 | 0x67 | 0x25 | 0x22 | 0xbd | 0x96 | 0x0 | 0x0 | 0x68 | 0x67 | 0x25 | 0x23 | 0x4a | 0x44 | 0x0 | 0x0 | 0x68 | 0x67 | 0x25 | 0x22 | 0xf6 | 0xa2 | 0x0 | 0x0 | 0x0 | 0x0 | 0x0 | 0x0 | 0x0 | 0x0 | 0x0 | 0x0 | 0x0 | 0x0 | 0x0 | 0x0 | 0x0 | 0x0 | 0x0 | 0x0 | 0
2026-04-10 10:46:32.531890 | 2026-04-10 10:46:35.858837 | 88554242140008 | 0x68 | 0x67 | 0x25 | 0x24 | 0x8a | 0x50 | 0x0 | 0x0 | 0x68 | 0x67 | 0x25 | 0x25 | 0xeb | 0x7e | 0x0 | 0x0 | 0x68 | 0x67 | 0x25 | 0x26 | 0x2 | 0x94 | 0x0 | 0x0 | 0x68 | 0x67 | 0x25 | 0x22 | 0xae | 0x16 | 0x0 | 0x0 | 0x58 | 0xcf | 0x79 | 0x38 | 0xe4 | 0x34 | 0x0 | 0x0 | 0x0 | 0x0 | 0x0 | 0x0 | 0x0 | 0x0 | 0x0 | 0x0 | 0x0 | 0x0 | 0x0 | 0x0 | 0x0 | 0x0 | 0x0 | 0x0 | 0
2026-04-10 10:46:32.531890 | 2026-04-10 10:46:35.858837 | 88996964847448 | 0x58 | 0xcf | 0x79 | 0x38 | 0xf1 | 0x50 | 0x0 | 0x0 | 0x58 | 0xcf | 0x79 | 0x38 | 0xe0 | 0x40 | 0x0 | 0x0 | 0x68 | 0x67 | 0x25 | 0x26 | 0xa0 | 0x32 | 0x0 | 0x0 | 0x0 | 0x0 | 0x0 | 0x0 | 0x0 | 0x0 | 0x0 | 0x0 | 0x58 | 0xcf | 0x79 | 0x38 | 0xe1 | 0xc8 | 0x0 | 0x0 | 0x0 | 0x0 | 0x0 | 0x0 | 0x0 | 0x0 | 0x0 | 0x0 | 0x0 | 0x0 | 0x0 | 0x0 | 0x0 | 0x0 | 0x0 | 0x0 | 0
2026-04-10 10:46:32.531890 | 2026-04-10 10:46:35.858837 | 13916266915688 | 0x68 | 0x67 | 0x25 | 0x22 | 0xa8 | 0xc | 0x0 | 0x0 | 0x58 | 0xcf | 0x79 | 0x38 | 0xe0 | 0x38 | 0x0 | 0x0 | 0x68 | 0x67 | 0x25 | 0x24 | 0xd9 | 0x2c | 0x0 | 0x0 | 0x68 | 0x67 | 0x25 | 0x22 | 0xf6 | 0xa2 | 0x0 | 0x0 | 0x60 | 0x55 | 0xf9 | 0xd9 | 0xe1 | 0xd6 | 0x0 | 0x0 | 0x0 | 0x0 | 0x0 | 0x0 | 0x0 | 0x0 | 0x0 | 0x0 | 0x0 | 0x0 | 0x0 | 0x0 | 0x0 | 0x0 | 0x0 | 0x0 | 0
2026-04-10 10:46:32.531890 | 2026-04-10 10:46:35.858837 | 209904264898408 | 0x68 | 0x67 | 0x25 | 0x25 | 0xe8 | 0xbe | 0x0 | 0x0 | 0x68 | 0x67 | 0x25 | 0x22 | 0xbb | 0xdc | 0x0 | 0x0 | 0x60 | 0x55 | 0xf9 | 0xd9 | 0xe1 | 0xd6 | 0x0 | 0x0 | 0x58 | 0xcf | 0x79 | 0x38 | 0xe0 | 0x38 | 0x0 | 0x0 | 0x0 | 0x0 | 0x0 | 0x0 | 0x0 | 0x0 | 0x0 | 0x0 | 0x0 | 0x0 | 0x0 | 0x0 | 0x0 | 0x0 | 0x0 | 0x0 | 0x0 | 0x0 | 0x0 | 0x0 | 0x0 | 0x0 | 0x0 | 0x0 | 0
2026-04-10 10:46:32.531890 | 2026-04-10 10:46:35.858837 | 2646323062632 | 0x68 | 0x67 | 0x25 | 0x25 | 0x68 | 0x2 | 0x0 | 0x0 | 0x68 | 0x67 | 0x25 | 0x22 | 0xb3 | 0xca | 0x0 | 0x0 | 0x68 | 0x67 | 0x25 | 0x23 | 0x77 | 0xfa | 0x0 | 0x0 | 0x68 | 0x67 | 0x25 | 0x25 | 0xf7 | 0x66 | 0x0 | 0x0 | 0x60 | 0x55 | 0xf9 | 0xd9 | 0x2d | 0x44 | 0x0 | 0x0 | 0x0 | 0x0 | 0x0 | 0x0 | 0x0 | 0x0 | 0x0 | 0x0 | 0x0 | 0x0 | 0x0 | 0x0 | 0x0 | 0x0 | 0x0 | 0x0 | 0
2026-04-10 10:46:32.531890 | 2026-04-10 10:46:35.858837 | 5403692066664 | 0x68 | 0x67 | 0x25 | 0x25 | 0xea | 0x4 | 0x0 | 0x0 | 0x58 | 0xcf | 0x79 | 0x38 | 0xe1 | 0xc8 | 0x0 | 0x0 | 0x58 | 0xcf | 0x79 | 0x38 | 0xde | 0x3e | 0x0 | 0x0 | 0x68 | 0x67 | 0x25 | 0x26 | 0xa0 | 0x32 | 0x0 | 0x0 | 0x68 | 0x67 | 0x25 | 0x23 | 0xa6 | 0x46 | 0x0 | 0x0 | 0x0 | 0x0 | 0x0 | 0x0 | 0x0 | 0x0 | 0x0 | 0x0 | 0x0 | 0x0 | 0x0 | 0x0 | 0x0 | 0x0 | 0x0 | 0x0 | 0
2026-04-10 10:46:32.531890 | 2026-04-10 10:46:35.858837 | 260434879434584 | 0x58 | 0xcf | 0x79 | 0x38 | 0xdd | 0xec | 0x0 | 0x0 | 0x0 | 0x0 | 0x0 | 0x0 | 0x0 | 0x0 | 0x0 | 0x0 | 0x0 | 0x0 | 0x0 | 0x0 | 0x0 | 0x0 | 0x0 | 0x0 | 0x0 | 0x0 | 0x0 | 0x0 | 0x0 | 0x0 | 0x0 | 0x0 | 0x0 | 0x0 | 0x0 | 0x0 | 0x0 | 0x0 | 0x0 | 0x0 | 0x58 | 0xcf | 0x79 | 0x38 | 0xdf | 0xea | 0x0 | 0x0 | 0x68 | 0x67 | 0x25 | 0x26 | 0xa0 | 0x32 | 0x0 | 0x0 | 0
2026-04-10 10:46:32.531890 | 2026-04-10 10:46:35.858837 | 258244446113624 | 0x58 | 0xcf | 0x79 | 0x38 | 0xdf | 0xea | 0x0 | 0x0 | 0x0 | 0x0 | 0x0 | 0x0 | 0x0 | 0x0 | 0x0 | 0x0 | 0x0 | 0x0 | 0x0 | 0x0 | 0x0 | 0x0 | 0x0 | 0x0 | 0x0 | 0x0 | 0x0 | 0x0 | 0x0 | 0x0 | 0x0 | 0x0 | 0x0 | 0x0 | 0x0 | 0x0 | 0x0 | 0x0 | 0x0 | 0x0 | 0x68 | 0x67 | 0x25 | 0x22 | 0xa0 | 0x2 | 0x0 | 0x0 | 0x58 | 0xcf | 0x79 | 0x38 | 0xdd | 0xec | 0x0 | 0x0 | 0
2026-04-10 10:46:32.531890 | 2026-04-10 10:46:35.858837 | 103380502800232 | 0x68 | 0x67 | 0x25 | 0x26 | 0x6 | 0x5e | 0x0 | 0x0 | 0x58 | 0xcf | 0x79 | 0x38 | 0xe1 | 0x1e | 0x0 | 0x0 | 0x60 | 0x55 | 0xf9 | 0xd9 | 0x2f | 0x6 | 0x0 | 0x0 | 0x68 | 0x67 | 0x25 | 0x24 | 0x43 | 0xb8 | 0x0 | 0x0 | 0x68 | 0x67 | 0x25 | 0x25 | 0xfd | 0x12 | 0x0 | 0x0 | 0x0 | 0x0 | 0x0 | 0x0 | 0x0 | 0x0 | 0x0 | 0x0 | 0x0 | 0x0 | 0x0 | 0x0 | 0x0 | 0x0 | 0x0 | 0x0 | 0
2026-04-10 10:46:32.531890 | 2026-04-10 10:46:35.858837 | 58154804694872 | 0x58 | 0xcf | 0x79 | 0x38 | 0xe4 | 0x34 | 0x0 | 0x0 | 0x68 | 0x67 | 0x25 | 0x22 | 0xa7 | 0x5a | 0x0 | 0x0 | 0x60 | 0x55 | 0xf9 | 0xda | 0x92 | 0x58 | 0x0 | 0x0 | 0x68 | 0x67 | 0x25 | 0x24 | 0x8a | 0x50 | 0x0 | 0x0 | 0x0 | 0x0 | 0x0 | 0x0 | 0x0 | 0x0 | 0x0 | 0x0 | 0x0 | 0x0 | 0x0 | 0x0 | 0x0 | 0x0 | 0x0 | 0x0 | 0x0 | 0x0 | 0x0 | 0x0 | 0x0 | 0x0 | 0x0 | 0x0 | 0
2026-04-10 10:46:32.531890 | 2026-04-10 10:46:35.858837 | 33952663981912 | 0x58 | 0xcf | 0x79 | 0x38 | 0xe1 | 0x1e | 0x0 | 0x0 | 0x68 | 0x67 | 0x25 | 0x22 | 0xb7 | 0x70 | 0x0 | 0x0 | 0x68 | 0x67 | 0x25 | 0x26 | 0x6 | 0x5e | 0x0 | 0x0 | 0x68 | 0x67 | 0x25 | 0x26 | 0x0 | 0xb6 | 0x0 | 0x0 | 0x68 | 0x67 | 0x25 | 0x22 | 0xab | 0xb0 | 0x0 | 0x0 | 0x0 | 0x0 | 0x0 | 0x0 | 0x0 | 0x0 | 0x0 | 0x0 | 0x0 | 0x0 | 0x0 | 0x0 | 0x0 | 0x0 | 0x0 | 0x0 | 0
2026-04-10 10:46:32.531890 | 2026-04-10 10:46:35.858837 | 108487168583528 | 0x68 | 0x67 | 0x25 | 0x23 | 0xab | 0x62 | 0x0 | 0x0 | 0x68 | 0x67 | 0x25 | 0x26 | 0x1 | 0x7a | 0x0 | 0x0 | 0x68 | 0x67 | 0x25 | 0x25 | 0xfb | 0x44 | 0x0 | 0x0 | 0x68 | 0x67 | 0x25 | 0x22 | 0xa0 | 0x58 | 0x0 | 0x0 | 0x68 | 0x67 | 0x25 | 0x26 | 0xa1 | 0x18 | 0x0 | 0x0 | 0x0 | 0x0 | 0x0 | 0x0 | 0x0 | 0x0 | 0x0 | 0x0 | 0x0 | 0x0 | 0x0 | 0x0 | 0x0 | 0x0 | 0x0 | 0x0 | 0
2026-04-10 10:46:32.531890 | 2026-04-10 10:46:35.858837 | 139548405622632 | 0x68 | 0x67 | 0x25 | 0x25 | 0xeb | 0x7e | 0x0 | 0x0 | 0x68 | 0x67 | 0x25 | 0x24 | 0xd9 | 0x2c | 0x0 | 0x0 | 0x68 | 0x67 | 0x25 | 0x24 | 0x8a | 0x50 | 0x0 | 0x0 | 0x68 | 0x67 | 0x25 | 0x23 | 0x8b | 0x44 | 0x0 | 0x0 | 0x68 | 0x67 | 0x25 | 0x22 | 0xa7 | 0x5a | 0x0 | 0x0 | 0x0 | 0x0 | 0x0 | 0x0 | 0x0 | 0x0 | 0x0 | 0x0 | 0x0 | 0x0 | 0x0 | 0x0 | 0x0 | 0x0 | 0x0 | 0x0 | 0
2026-04-10 10:46:32.531890 | 2026-04-10 10:46:35.858837 | 97449085855592 | 0x68 | 0x67 | 0x25 | 0x22 | 0xa1 | 0x58 | 0x0 | 0x0 | 0x60 | 0x55 | 0xf9 | 0xd9 | 0x2d | 0xac | 0x0 | 0x0 | 0x68 | 0x67 | 0x25 | 0x22 | 0xad | 0x6a | 0x0 | 0x0 | 0x68 | 0x67 | 0x25 | 0x25 | 0xf1 | 0xd2 | 0x0 | 0x0 | 0x68 | 0x67 | 0x25 | 0x24 | 0xd9 | 0x9c | 0x0 | 0x0 | 0x0 | 0x0 | 0x0 | 0x0 | 0x0 | 0x0 | 0x0 | 0x0 | 0x0 | 0x0 | 0x0 | 0x0 | 0x0 | 0x0 | 0x0 | 0x0 | 0
2026-04-10 10:46:32.531890 | 2026-04-10 10:46:35.858837 | 222724725499752 | 0x68 | 0x67 | 0x25 | 0x24 | 0x91 | 0xca | 0x0 | 0x0 | 0x0 | 0x0 | 0x0 | 0x0 | 0x0 | 0x0 | 0x0 | 0x0 | 0x68 | 0x67 | 0x25 | 0x22 | 0xbb | 0xdc | 0x0 | 0x0 | 0x68 | 0x67 | 0x25 | 0x22 | 0xbb | 0xaa | 0x0 | 0x0 | 0x0 | 0x0 | 0x0 | 0x0 | 0x0 | 0x0 | 0x0 | 0x0 | 0x0 | 0x0 | 0x0 | 0x0 | 0x0 | 0x0 | 0x0 | 0x0 | 0x0 | 0x0 | 0x0 | 0x0 | 0x0 | 0x0 | 0x0 | 0x0 | 0
2026-04-10 10:46:32.531890 | 2026-04-10 10:46:35.858837 | 123931854202728 | 0x68 | 0x67 | 0x25 | 0x22 | 0xb7 | 0x70 | 0x0 | 0x0 | 0x68 | 0x67 | 0x25 | 0x25 | 0xe7 | 0x8a | 0x0 | 0x0 | 0x58 | 0xcf | 0x79 | 0x38 | 0xe1 | 0x1e | 0x0 | 0x0 | 0x68 | 0x67 | 0x25 | 0x26 | 0x7f | 0x98 | 0x0 | 0x0 | 0x68 | 0x67 | 0x25 | 0x25 | 0xe5 | 0x8 | 0x0 | 0x0 | 0x0 | 0x0 | 0x0 | 0x0 | 0x0 | 0x0 | 0x0 | 0x0 | 0x0 | 0x0 | 0x0 | 0x0 | 0x0 | 0x0 | 0x0 | 0x0 | 0
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

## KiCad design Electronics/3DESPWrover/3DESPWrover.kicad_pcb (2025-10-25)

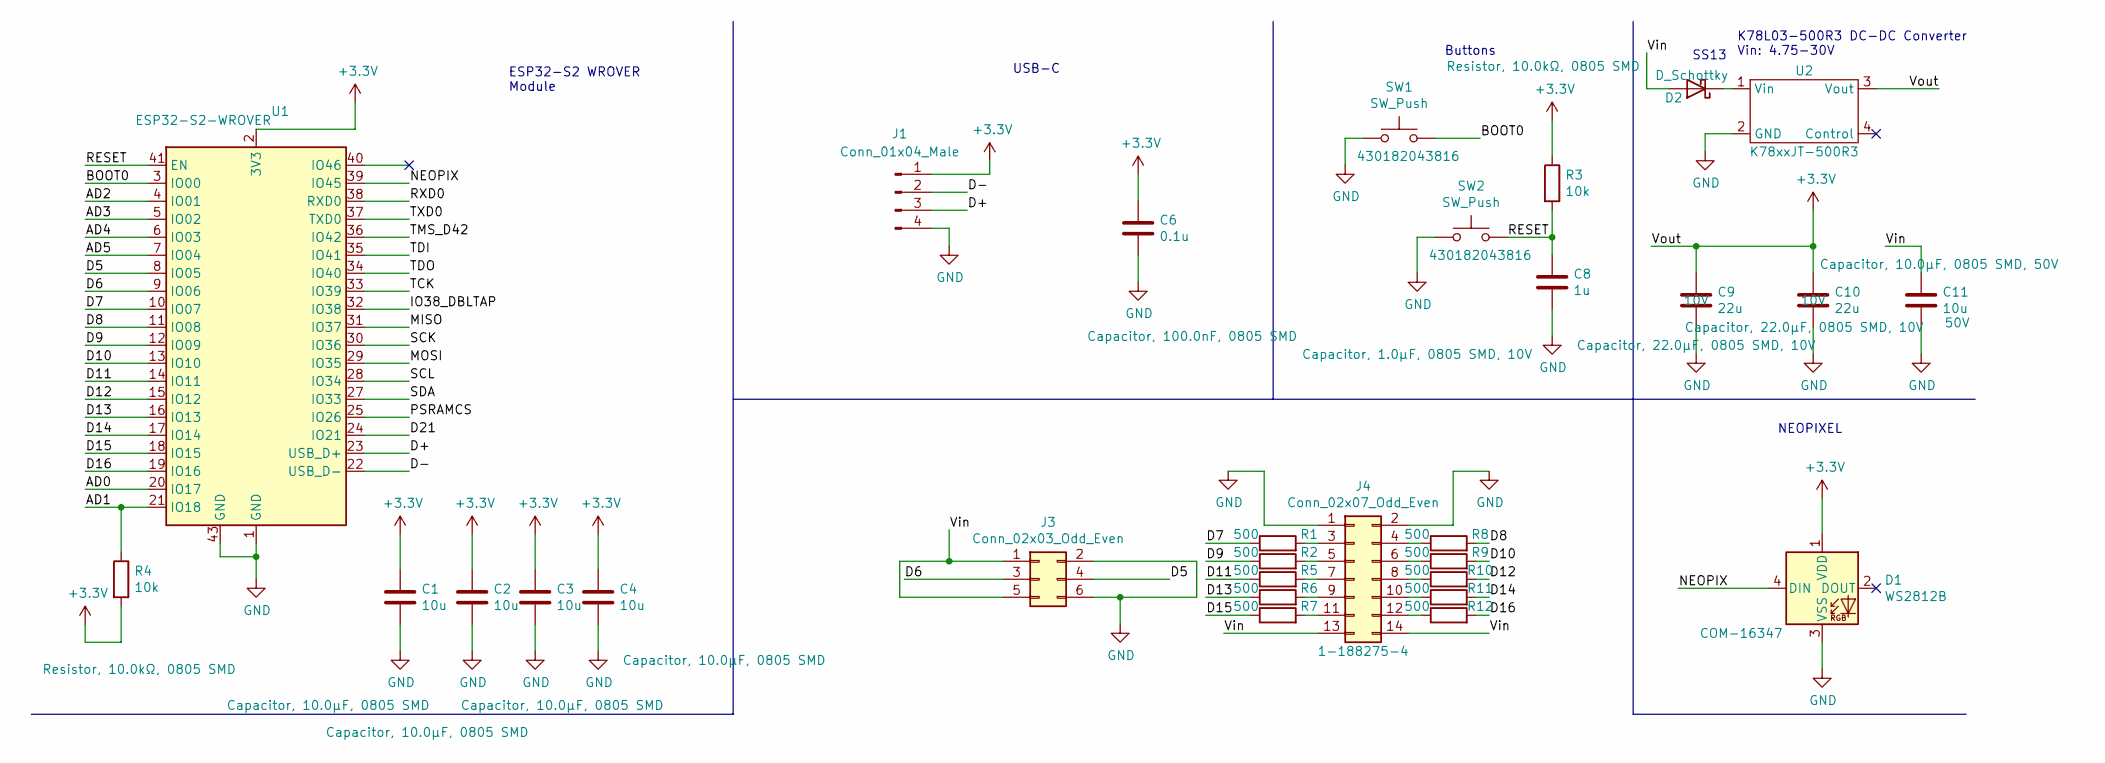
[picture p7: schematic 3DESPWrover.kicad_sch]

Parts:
C1, C2, C3, C4: 10u; C_0805_2012Metric_Pad1.18x1.45mm_HandSolder; MPN Capacitor, 10.0µF, 0805 SMD
C6: 0.1u; C_0805_2012Metric_Pad1.18x1.45mm_HandSolder; MPN Capacitor, 100.0nF, 0805 SMD
C8: 1u; C_0805_2012Metric_Pad1.18x1.45mm_HandSolder; MPN Capacitor, 1.0µF, 0805 SMD, 10V
C9, C10: 22u; C_0805_2012Metric_Pad1.18x1.45mm_HandSolder; Voltage 10V; MPN Capacitor, 22.0µF, 0805 SMD, 10V
C11: 10u; C_0805_2012Metric_Pad1.18x1.45mm_HandSolder; Voltage 50V; MPN Capacitor, 10.0µF, 0805 SMD, 50V
D1: WS2812B; LED_WS2812B_PLCC4_5.0x5.0mm_P3.2mm; MPN COM-16347
D2: D_Schottky; D_SMA; MPN SS13
J1: Conn_01x04_Male; PinHeader_1x04_P2.54mm_Vertical; MPN 0022052041
J3: Conn_02x03_Odd_Even; PinHeader_2x03_P2.54mm_Vertical; MPN SSW-103-01-F-D
J4: Conn_02x07_Odd_Even; TE_Micromatch_2,54_14_SMD; MPN 1-188275-4
R1, R2, R5, R6, R7, R8, R9, R10, R11, R12: 500; R_0603_1608Metric_Pad0.98x0.95mm_HandSolder; MPN Resistor, 510.0Ω, 0603 SMD
R3, R4: 10k; R_0805_2012Metric_Pad1.20x1.40mm_HandSolder; MPN Resistor, 10.0kΩ, 0805 SMD
SW1, SW2: SW_Push; SW_SPST_B3S-1000; MPN 430182043816
U1: ESP32-S2-WROVER; MPN DFR0743-WROVER
U2: K78xxJT-500R3; K7803JT-500R3-SMD; MPN K7803JT-500R3

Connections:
+3V3: C1.1, C2.1, C3.1, C4.1, C6.1, C9.1, C10.1, D1.1 (VDD), J1.1, R3.1, R4.2, U1.2 (3V3), U2.3 (Vout)
/AD0: U1.20 (IO17)
/AD1: R4.1, U1.21 (IO18)
/AD2: U1.4 (IO01)
/AD3: U1.5 (IO02)
/AD4: U1.6 (IO03)
/AD5: U1.7 (IO04)
/BOOT0: SW1.2, U1.3 (IO00)
/D5: J3.4, U1.8 (IO05)
/D6: J3.3, U1.9 (IO06)
/D7: R1.1, U1.10 (IO07)
/D8: R8.2, U1.11 (IO08)
/D9: R2.1, U1.12 (IO09)
/D10: R9.2, U1.13 (IO10)
/D11: R5.1, U1.14 (IO11)
/D12: R10.2, U1.15 (IO12)
/D13: R6.1, U1.16 (IO13)
/D14: R11.2, U1.17 (IO14)
/D15: R7.1, U1.18 (IO15)
/D16: R12.2, U1.19 (IO16)
/D21: U1.24 (IO21)
/D+: J1.3, U1.23 (USB_D+)
/D-: J1.2, U1.22 (USB_D-)
/IO38_DBLTAP: U1.32 (IO38)
/MISO: U1.31 (IO37)
/MOSI: U1.29 (IO35)
/NEOPIX: D1.4 (DIN), U1.39 (IO45)
/PSRAMCS: U1.25 (IO26)
/RESET: C8.1, R3.2, SW2.2, U1.41 (EN)
/RXD0: U1.38 (RXD0)
/SCK: U1.30 (IO36)
/SCL: U1.28 (IO34)
/SDA: U1.27 (IO33)
/TCK: U1.33 (IO39)
/TDI: U1.35 (IO41)
/TDO: U1.34 (IO40)
/TMS_D42: U1.36 (IO42)
/TXD0: U1.37 (TXD0)
/Vin: C11.1, D2.2 (A), J3.1, J3.5, J4.13, J4.14
GND: C1.2, C2.2, C3.2, C4.2, C6.2, C8.2, C9.2, C10.2, C11.2, D1.3 (VSS), J1.4, J3.2, J3.6, J4.1, J4.2, SW1.1, SW2.1, U1.1 (GND), U1.26 (GND), U1.42 (GND), U1.43 (GND), U1.44 (GND), U1.45 (GND), U1.46 (GND), U1.47 (GND), U1.48 (GND), U1.49 (GND), U1.50 (GND), U1.51 (GND), U2.2 (GND)
unnamed: D2.1 (K), U2.1 (Vin)
unnamed: J4.3, R1.2
unnamed: J4.4, R8.1
unnamed: J4.5, R2.2
unnamed: J4.6, R9.1
unnamed: J4.7, R5.2
unnamed: J4.8, R10.1
unnamed: J4.9, R6.2
unnamed: J4.10, R11.1
unnamed: J4.11, R7.2
unnamed: J4.12, R12.1

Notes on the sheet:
Buttons
K78L03-500R3 DC-DC Converter Vin: 4.75-30V
NEOPIXEL
ESP32-S2 WROVER Module
USB-C
SS13

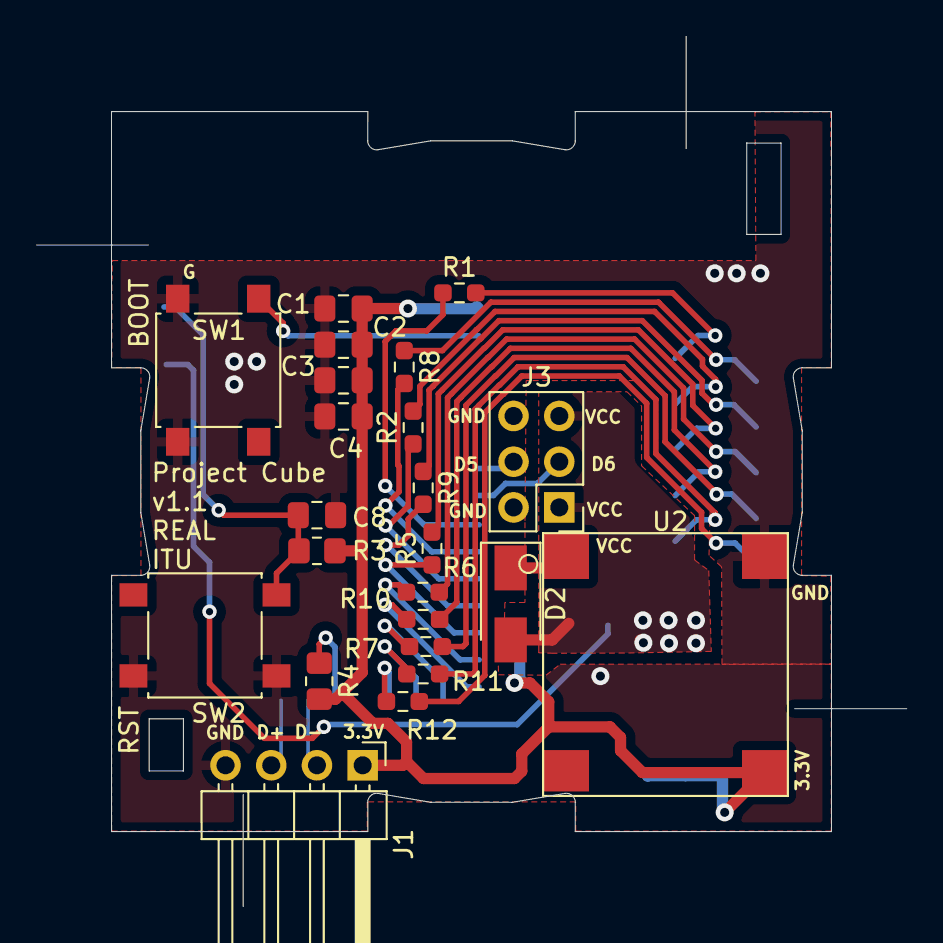
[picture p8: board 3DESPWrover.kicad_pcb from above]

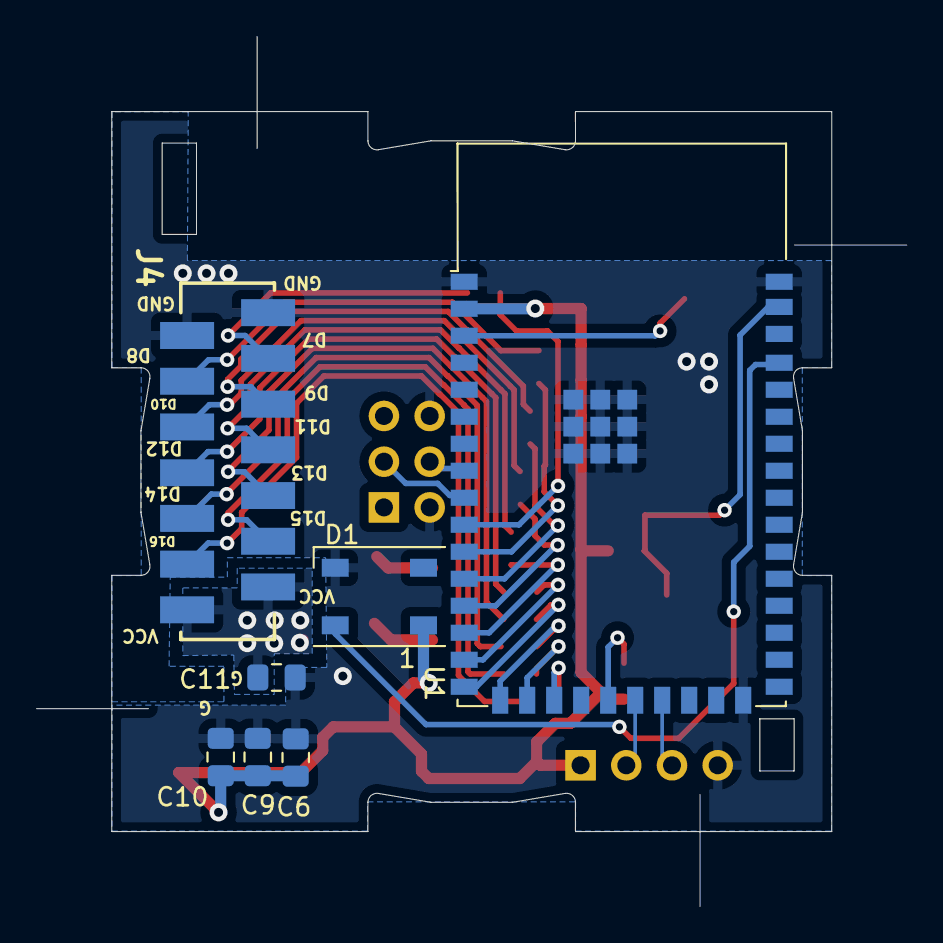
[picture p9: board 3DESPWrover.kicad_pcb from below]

Board: 2 copper layers, 40.0 x 40.0 mm, 30 parts (7 on the bottom side), 32 nets.

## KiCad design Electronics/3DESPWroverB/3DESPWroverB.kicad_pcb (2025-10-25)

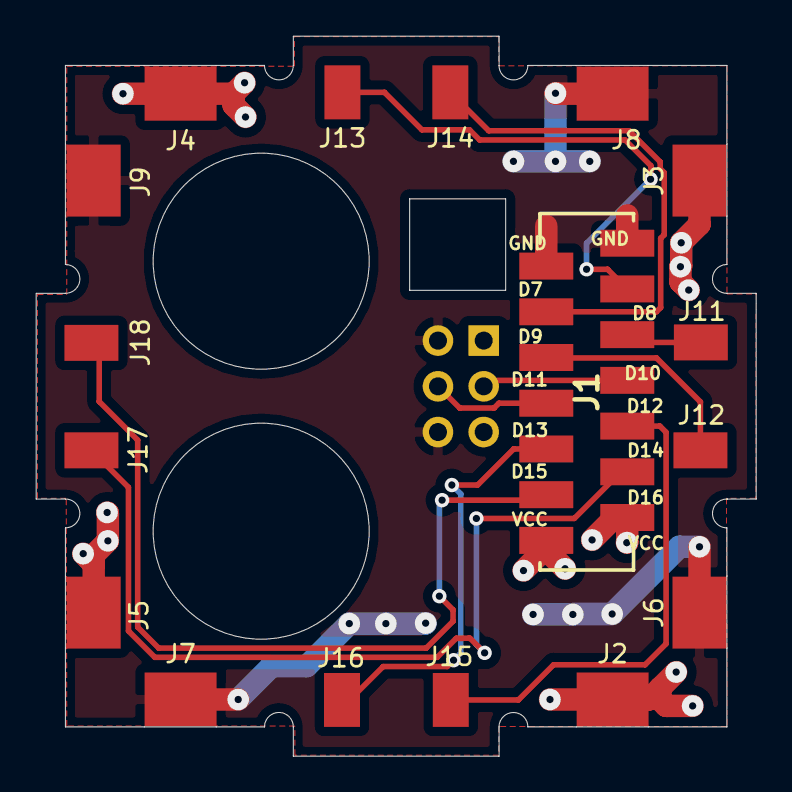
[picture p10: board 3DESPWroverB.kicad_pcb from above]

Board: 2 copper layers, 40.0 x 40.0 mm, 18 parts (1 on the bottom side), 12 nets.

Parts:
J1: Conn_02x07_Odd_Even; TE_Micromatch_2,54_14_SMD
J2, J3, J4, J5, J6, J7, J8, J9: Conn_01x01; CubeSidePad
J10: Conn_02x03_Odd_Even; PinHeader_2x03_P2.54mm_Vertical
J11, J12, J13, J14, J15, J16, J17, J18: Conn_01x01; CubeCenterPad

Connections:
/D7: J1.3, J13.1
/D8: J1.4, J14.1
/D9: J1.5, J11.1
/D10: J1.6, J12.1
/D11: J1.7, J10.3
/D12: J1.8, J10.4
/D13: J1.9, J15.1
/D14: J1.10, J16.1
/D15: J1.11, J17.1
/D16: J1.12, J18.1
GND: J1.1, J1.2, J6.1, J7.1, J8.1, J9.1, J10.2, J10.6
VCC: J1.13, J1.14, J2.1, J3.1, J4.1, J5.1, J10.1, J10.5

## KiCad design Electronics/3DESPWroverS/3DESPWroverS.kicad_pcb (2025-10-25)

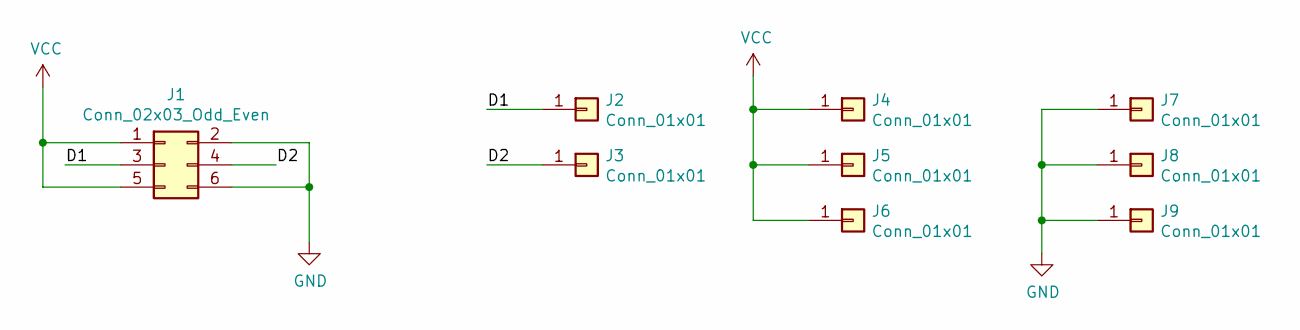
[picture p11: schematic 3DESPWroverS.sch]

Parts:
J1: Conn_02x03_Odd_Even; PinHeader_2x03_P2.54mm_Vertical
J2, J3: Conn_01x01; CubeCenterPad
J4, J5, J6, J7, J8, J9: Conn_01x01; CubeSidePad

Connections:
/D1: J1.3, J2.1
/D2: J1.4, J3.1
GND: J1.2, J1.6, J7.1, J8.1, J9.1
VCC: J1.1, J1.5, J4.1, J5.1, J6.1

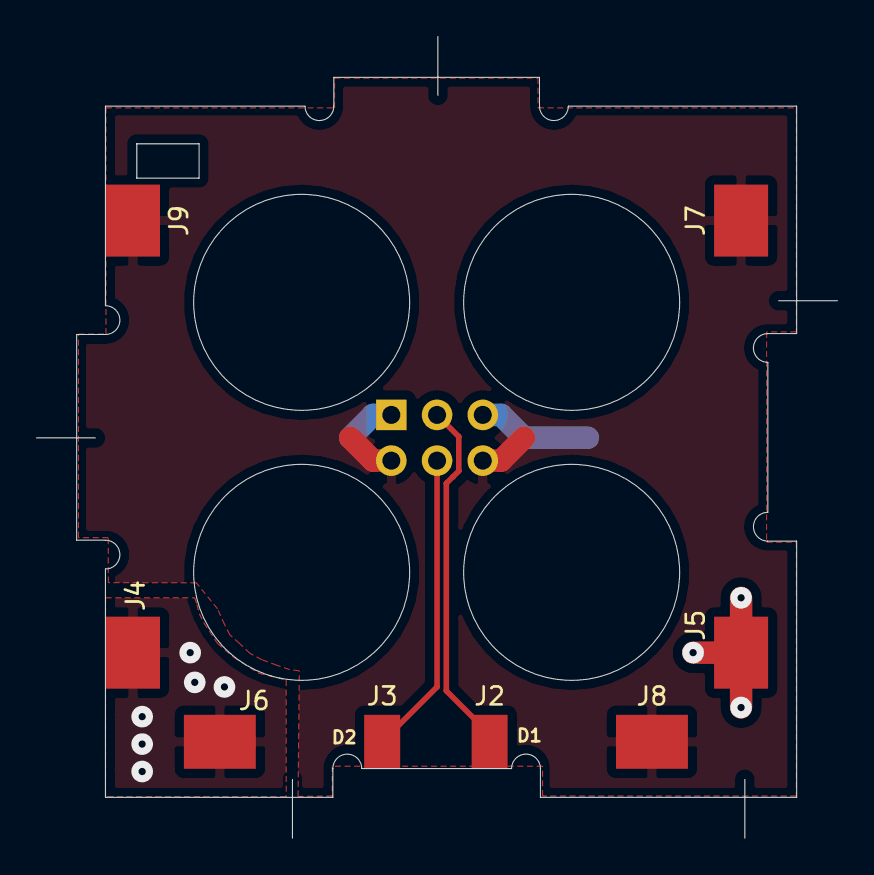
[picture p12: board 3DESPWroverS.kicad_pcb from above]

Board: 2 copper layers, 40.0 x 40.0 mm, 9 parts (1 on the bottom side), 4 nets.

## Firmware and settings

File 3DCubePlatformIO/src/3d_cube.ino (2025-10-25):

/* Cubes_3D Main File
**
** Author: kwal@itu.dk (WITH ASSISTANCE FROM lukeawalker@hotmail.co.uk)
** Date:   11/14/2022
**
** Coding standards:
**    braces {
**        Indent - 4 spaces
**    }
**    variable_names
**    CONSTANT_NAMES (including #defines)
**    functionNames
**    ClassNames
**    Line length - max 100 characters
*/

/***************************************************************************************************
** INCLUDES
***************************************************************************************************/

/* First put c/c++ standard headers */
#include <stdint.h>
#include "driver/ledc.h"
#include <WiFi.h>
#include <HTTPClient.h>
// #include <ESPmDNS.h>
// #include <WiFiUdp.h>
#include <Adafruit_NeoPixel.h>
#include <math.h>
// #include <AsyncTCP.h>
#include <ESPAsyncWebServer.h>
#include <AsyncElegantOTA.h>
#include "AsyncJson.h"
#include "ArduinoJson.h"
//#include <HTTPClient.h>
#include <StreamUtils.h>
#include <ESPmDNS.h>
#include <Preferences.h>

/* Then library headers */
#include "Arduino.h"

/* lastly our own headers */
#include "neural_network.h"
//#include "fake_nn.h"
#include "neural_damage.h" //DAMAGE DEBUG

/***************************************************************************************************
** DEFINES
***************************************************************************************************/

/* Program selector */
#define ALL
// #define PULSE_TEST

/* Timer variables */
#define TIMER_0 0
#define PRESCALER_1MHZ 80
#define COUNT_UP true,

#define MAX_MESSAGE_FLOAT_LENGTH 28
#define MAX_MESSAGE_BYTE_LENGTH MAX_MESSAGE_FLOAT_LENGTH*4
#define MESSAGE_GAP_US 1000
#define MESSAGE_TIMESCALER 41 // 118 AT 30HZ
#define MESSAGE_DUTYSCALER 806
#define MESSAGE_OFFSET 403 // MESSAGE_DUTYSCALER/2
#define MESSAGE_FREQUENCY 2400 // HZ
#define MESSAGE_REPETITIONS 3

#define HEADER_MESSAGE 6
//#define INTERRUPT_MESSAGE 9
#define MAX_MESSAGE_DUTY 10
#define ONE_LENGTH 4
#define ZERO_LENGTH 2

#define OFFSET_FACTOR 127
#define SCALE_FACTOR 2//10
#define MAX_MESSAGE_RAW 255.0


#define UPDATE_TIMEOUT_MS 3000
#define MAX_UPDATES 90

#define LED_PIN 45
#define LED_COUNT 1

#define FORMAT_SPIFFS_IF_FAILED true

/***************************************************************************************************
** TYPEDEFS
***************************************************************************************************/

typedef enum
{
    PWM_READY = 0,
    PWM_STARTED,
    PWM_ENDED,
    HEADER_READY,
    HEADER_STARTED,
    HEADER_ENDED,
} pwm_send_state_t;

/***************************************************************************************************
** ENUMS
***************************************************************************************************/

enum
{
    EAST = 0,
    WEST,
    NORTH,
    SOUTH,
    FRONT,
    BACK,
    NUM_DIRECTIONS,
};

/***************************************************************************************************
** CLASSES
***************************************************************************************************/
class Neighborhood
{
public:
    uint16_t east0 = 0;
    uint16_t east1 = 0;
    uint16_t east2 = 0;
    uint16_t east3 = 0;
    uint16_t east4 = 0;
    uint16_t east5 = 0;
    uint16_t east6 = 0;
    uint16_t east7 = 0;

    uint16_t west0 = 0;
    uint16_t west1 = 0;
    uint16_t west2 = 0;
    uint16_t west3 = 0;
    uint16_t west4 = 0;
    uint16_t west5 = 0;
    uint16_t west6 = 0;
    uint16_t west7 = 0;

    uint16_t north0 = 0;
    uint16_t north1 = 0;
    uint16_t north2 = 0;
    uint16_t north3 = 0;
    uint16_t north4 = 0;
    uint16_t north5 = 0;
    uint16_t north6 = 0;
    uint16_t north7 = 0;

    uint16_t south0 = 0;
    uint16_t south1 = 0;
    uint16_t south2 = 0;
    uint16_t south3 = 0;
    uint16_t south4 = 0;
    uint16_t south5 = 0;
    uint16_t south6 = 0;
    uint16_t south7 = 0;

    uint16_t front0 = 0;
    uint16_t front1 = 0;
    uint16_t front2 = 0;
    uint16_t front3 = 0;
    uint16_t front4 = 0;
    uint16_t front5 = 0;
    uint16_t front6 = 0;
    uint16_t front7 = 0;

    uint16_t back0 = 0;
    uint16_t back1 = 0;
    uint16_t back2 = 0;
    uint16_t back3 = 0;
    uint16_t back4 = 0;
    uint16_t back5 = 0;
    uint16_t back6 = 0;
    uint16_t back7 = 0;
};

class FloatData
{
public:
    /*******************************************************************************************
    ** METHODS
    *******************************************************************************************/
    FloatData()
    {
    }

    union ByteToFloat
   {
    uint8_t byteData[4];     
    float floatData; 
   };

    FloatData(float *new_message)
    {
        for (int i = 0; i < MAX_MESSAGE_FLOAT_LENGTH; i++)
        {
            message[i] = new_message[i];
        }
    }

    void fromRaw(uint16_t *raw_data)
    {
        for (int i = 0; i < MAX_MESSAGE_FLOAT_LENGTH; i++)
        {
            ByteToFloat converter;
            converter.byteData[0] = raw_data[i*4];
            converter.byteData[1] = raw_data[i*4+1];
            converter.byteData[2] = raw_data[i*4+2];
            converter.byteData[3] = raw_data[i*4+3];
            message[i] = converter.floatData;
        }
    }

    void toRaw(uint8_t *raw_data)
    {
        for (int i = 0; i < MAX_MESSAGE_FLOAT_LENGTH; i++)
        {   
            ByteToFloat converter;
            converter.floatData = message[i];
            raw_data[i*4] = converter.byteData[0];
            raw_data[i*4+1] = converter.byteData[1];
            raw_data[i*4+2] = converter.byteData[2];
            raw_data[i*4+3] = converter.byteData[3];
        }
    }

    /*******************************************************************************************
    ** MEMBERS
    *******************************************************************************************/
    float message[MAX_MESSAGE_FLOAT_LENGTH] = {0.0};
};

class PwmRxData
{
public:
    /*******************************************************************************************
    ** METHODS
    *******************************************************************************************/
    PwmRxData(int rx_pin)
    {
        pin = rx_pin;
    }

    bool complete()
    {
        return message_pos >= MAX_MESSAGE_BYTE_LENGTH;
    }

    /* Set once when the message completes. Reset by a read to this function (or a reset) */
    bool hasCompleted()
    {
        bool temp = has_completed;
        has_completed = false;
        return temp;
    }

    void reset()
    {
        message_pos = 0;
        start_time = 0;
        end_time = 0;
        has_completed = false;
        started = false;
        header_received = false;
        raw_pos = 0;
        bit_pos = 0;
        //interrupt_received = false;
    }

    uint8_t modifyBit(uint8_t inputByte,uint8_t position, uint8_t bitValue){
        uint8_t outputByte = 0;
        if(bitValue>=1){
            outputByte = inputByte | (1 << position);  // for setting the bit
        }else{      
            outputByte = inputByte & ~(1 << position); // for clearing the bit
        }
        return outputByte;
    }

    void handleRxInterrupt()
    {
        /* Only increment the message if we've not finished yet. This prevents old data being
        ** overwritten before we have a chance to read it */
        if (digitalRead(pin) == HIGH)
        {
            start_time = micros();
            started = true;
        }
        if (digitalRead(pin) == LOW and started == true)
        {
            //if (interrupt_received)
            //{
            //    started = false;
            //    return;
            //}
            //else
            //{
                // Serial.println("Interrupted LOW");
                end_time = micros();
                long elapsedTime = (end_time - start_time);

                //if ((elapsedTime > floor((INTERRUPT_MESSAGE - 0.5) * MESSAGE_TIMESCALER) && (elapsedTime < (MAX_MESSAGE_DUTY)*MESSAGE_TIMESCALER)))
                //{
                //    interrupt_received = true;
                //}

                if (!complete())
                {
                    if (!header_received)
                    {
                        // Serial.print("Header lenght ");
                        // Serial.println(header);
                        if (elapsedTime > floor((HEADER_MESSAGE - 0.5) * MESSAGE_TIMESCALER))
                        {
                            header_received = true;
                            rawMicroseconds[raw_pos++] = elapsedTime;
                        }
                    }
                    else
                    {
                        rawMicroseconds[raw_pos++] = elapsedTime;
                        // message[message_pos++] = elapsedTime / MESSAGE_TIMESCALER;

                        if (elapsedTime > floor((HEADER_MESSAGE - 0.5) * MESSAGE_TIMESCALER))
                        {
                            reset();
                        }
                        else
                        {
                            uint8_t receivedValue = 0;
                            if (elapsedTime > floor(MESSAGE_TIMESCALER * (ONE_LENGTH - 0.5)))
                            {
                                receivedValue = 1;
                            }

                            messageByteBuffer = modifyBit(messageByteBuffer, bit_pos, receivedValue);

                            if (bit_pos >= 7)
                            {
                                message[message_pos++] = messageByteBuffer;
                                bit_pos = 0;
                                messageByteBuffer = 0;
                            }
                            else
                            {
                                bit_pos++;
                            }
                        }
                    }

                    if (complete())
                    {
                        has_completed = true;
                        // header_received = false;
                    }
                }
                started = false;
            //}
        }
    }

    /*******************************************************************************************
    ** MEMBERS
    *******************************************************************************************/
    int pin;

    uint32_t start_time = 0;
    uint32_t end_time = 0;
    uint8_t bit_pos = 0;
    uint8_t message_pos = 0;
    uint16_t header = 0;
    uint16_t raw_pos = 0;

    bool has_completed = false;
    bool started = false;
    bool header_received = false;
    //bool interrupt_received = false;

    /* Message information limited to 8-bits in micros. Used 16-bits to account for potential
    ** noise */
    uint8_t messageByteBuffer = 0;
    uint16_t message[MAX_MESSAGE_BYTE_LENGTH] = {0};
    uint16_t rawMicroseconds[MAX_MESSAGE_BYTE_LENGTH*8 + 1] = {0};
};
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
void loop()
{

#if defined(ALL)
    /* Real program */

    for (int i = 0; i < NUM_DIRECTIONS; i++)
    {
        if (pwm_rx_data[i].complete() && !getNeighbors)
        {

            // Check message values to determine if a neighbors message is being received
            bool check100s = true;

            for (int j = MAX_MESSAGE_BYTE_LENGTH - 1; j > MAX_MESSAGE_BYTE_LENGTH - 11; j--)
            {
                if (pwm_rx_data[i].message[j] != 100)
                {
                    check100s = false;
                }
            }

            if (check100s)
            {
                interrupt_message_received = true;
            }
        }
    }

    //External button pressed  or interrupt header received
    if(button_pressed || interrupt_message_received){
        // if (!getNeighbors)
        // {
        //     for (int i = 0; i < NUM_DIRECTIONS; i++)
        //     {
        //         pwm_tx_data[i].reset();
        //     }

        //     // Send interrrupt header
        //     long delayLapse = 5000;
        //     long startTime = millis();
        //     long elapsed = millis() - startTime;
        //     bool blink = true;
        //     long interval = startTime;
        //     while (elapsed < delayLapse)
        //     {
        //         // for (int i = 0; i < NUM_DIRECTIONS; i++)
        //         // {
        //         //     pwm_tx_data[i].sendInterruptMessage();
        //         // }
        //         if ((millis() - interval) > 100)
        //         {
        //             for (int i = 0; i < NUM_DIRECTIONS; i++)
        //             {
        //                 pwm_tx_data[i].reset();
        //             }
        //             if (blink)
        //             {
        //                 colorWipe(strip.Color(225 / 2, 225 / 2, 0)); // yellow
        //                 blink = false;
        //             }
        //             else
        //             {
        //                 colorWipe(strip.Color(0, 0, 0));
        //                 blink = true;
        //             }
        //             interval = millis();
        //         }
        //         elapsed = millis() - startTime;
        //     }
        // }
        // for (int i = 0; i < NUM_DIRECTIONS; i++)
        //     {
        //         pwm_rx_data[i].reset();
        //     }
        if (button_pressed)
        {
            if (!getNeighbors)
            {
                // Set resetBuffers, idle_state and getNeighbors flags
                resetBuffers = true;
                getNeighbors = true;
                data_sent = true;
            }
            else
            {
                resetBuffers = false;
                getNeighbors = false;
                idle_state = true;
            }
        }else if(interrupt_message_received){
                resetBuffers = true;
                getNeighbors = true;
                data_sent = true;
        }
        //If it was button pressed, toggle getNeighbors in flash
        Serial.println("Interrupted");
        button_pressed=false;
        interrupt_message_received = false;
    }
    

    if (fail)
    {
        UPDATE_NUM = MAX_UPDATES + 1;
        //getNeighbors = false;
        if (!getNeighbors)
        {
            for (int i = 0; i < NUM_DIRECTIONS; i++)
            {
                pwm_rx_data[i].reset();
            }
        }

        colorWipe(strip.Color(255 / 2, 0, 0)); // red
        delay(300);
        if (millis() > 410000)
        { // Just for showing it is failing in the videos
            idle_state = true;
        }      
    }

    if (idle_state)
    {
        UPDATE_NUM = MAX_UPDATES + 1;
        //fail = false;
        colorWipe(strip.Color(0, 0, 255 / 2)); // blue
        delay(300);
        colorWipe(strip.Color(0, 0, 0));
        delay(300);

        if (!connected)
        {
            long randInit = random(0, 5000);
            delay(randInit);

            WiFi.begin(ssid, password);
            // WiFi.config(ip,gateway,subnet);

            Serial.println("");
            uint8_t connect_try_counter = 0;

            // Wait for connection;
            unsigned long startConnection = millis();
            while (WiFi.status() != WL_CONNECTED)
            {
                randInit = random(0, 500);
                delay(500 + randInit);
                colorWipe(strip.Color(255 / 2, 0, 0));
                Serial.print(".");
                delay(500 + randInit);
                colorWipe(strip.Color(0, 0, 0));
                Serial.print(".");
                if (WiFi.status() != WL_CONNECTED && (millis() - startConnection) > timeoutLength)
                {
                    //Flash
                    startConnection = millis();
                    delay(500);
                    colorWipe(strip.Color(0, 0, 255 / 2));
                    Serial.print(".");
                    delay(500);
                    colorWipe(strip.Color(0, 0, 0));
                    Serial.print(".");
                    if(connect_try_counter>=1){
                        //Save in flash and restart
                        preferences.begin("cube", false);
                        
                        if(getNeighbors){
                            bool neighborsFlagInMemory = preferences.getBool("neighbors", false);
                            if(!neighborsFlagInMemory){
                                preferences.putBool("neighbors", true);
                            }
                        }else if (!send_backup)
                        {
                            Serial.println("Creating backup");

                            //preferences.begin("cube", false);

                            preferences.putBytes("times", times, sizeof(times));
                            preferences.putBytes("guesses", guesses, sizeof(guesses));

                            for (int i = 0; i < MAX_UPDATES; i++)
                            {
                                preferences.putBytes("updates" + i, channel_updates[i], sizeof(channel_updates[i]));
                            }

                            Serial.println("Setting backup flag");
                            preferences.putBool("backup", true);

                        }

                          preferences.end();

                          delay(1000);

                          ESP.restart();
                    }
                    connect_try_counter +=1;
                    //Connection failed retrying
                    WiFi.reconnect();
                }
            }

            WiFi.setSleep(false);
            Serial.println("");
            Serial.print("Connected to ");
            Serial.println(ssid);
            Serial.print("IP address: ");
            Serial.println(WiFi.localIP());

            createServerEndpoints(server);
            AsyncElegantOTA.begin(&server); // Start ElegantOTA
            server.begin();
            Serial.println("HTTP server started");
            connected = true;
            

        }

        if((!data_sent && connected) && !getNeighbors){
            
            Serial.print("Service at ");
            Serial.println(database_ip);

            client.setTimeout(5);

            //if (!client.connect(database_ip.toString().c_str(), 8000)) {
            if(!http.begin(client, "http://"+database_ip.toString()+":8000/status_result")) {
                data_sent= false;
                Serial.println(F("Connection to status server failed"));
                send_attempts +=1;
            }else{

                DynamicJsonDocument doc(49152); //49152
                // StaticJsonDocument<49152> doc;

                doc["macId"] = macId;
                doc["fail_state"] = fail;
                doc["firmware"] = firmware_version;
                doc["damage_mode"] = damage_mode;
                doc["damage_class"] = damage_class;

                JsonArray update_times = doc.createNestedArray("update_times");
                for (int i = 0; i < MAX_UPDATES; i++)
                {
                    update_times.add(times[i]);
                }

                JsonArray state_guesses = doc.createNestedArray("state_guesses");
                for (int i = 0; i < MAX_UPDATES; i++)
                {
                    state_guesses.add(guesses[i]);
                }

                JsonArray cell_updates = doc.createNestedArray("cell_updates");
                for (int i = 0; i < MAX_UPDATES; i++)
                {
                    JsonArray cell_updates_row = cell_updates.createNestedArray();
                    for (int j = 0; j < MAX_MESSAGE_FLOAT_LENGTH; j++)
                    {
                        cell_updates_row.add(channel_updates[i][j]);
                    }
                }
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

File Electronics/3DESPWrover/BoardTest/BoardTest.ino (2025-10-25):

// A basic everyday NeoPixel strip test program.

// NEOPIXEL BEST PRACTICES for most reliable operation:
// - Add 1000 uF CAPACITOR between NeoPixel strip's + and - connections.
// - MINIMIZE WIRING LENGTH between microcontroller board and first pixel.
// - NeoPixel strip's DATA-IN should pass through a 300-500 OHM RESISTOR.
// - AVOID connecting NeoPixels on a LIVE CIRCUIT. If you must, ALWAYS
//   connect GROUND (-) first, then +, then data.
// - When using a 3.3V microcontroller with a 5V-powered NeoPixel strip,
//   a LOGIC-LEVEL CONVERTER on the data line is STRONGLY RECOMMENDED.
// (Skipping these may work OK on your workbench but can fail in the field)

#include <Adafruit_NeoPixel.h>
#ifdef __AVR__
 #include <avr/power.h> // Required for 16 MHz Adafruit Trinket
#endif

// Which pin on the Arduino is connected to the NeoPixels?
// On a Trinket or Gemma we suggest changing this to 1:
#define LED_PIN    45

// How many NeoPixels are attached to the Arduino?
#define LED_COUNT 1

// Declare our NeoPixel strip object:
Adafruit_NeoPixel strip(LED_COUNT, LED_PIN, NEO_GRB + NEO_KHZ800);
// Argument 1 = Number of pixels in NeoPixel strip
// Argument 2 = Arduino pin number (most are valid)
// Argument 3 = Pixel type flags, add together as needed:
//   NEO_KHZ800  800 KHz bitstream (most NeoPixel products w/WS2812 LEDs)
//   NEO_KHZ400  400 KHz (classic 'v1' (not v2) FLORA pixels, WS2811 drivers)
//   NEO_GRB     Pixels are wired for GRB bitstream (most NeoPixel products)
//   NEO_RGB     Pixels are wired for RGB bitstream (v1 FLORA pixels, not v2)
//   NEO_RGBW    Pixels are wired for RGBW bitstream (NeoPixel RGBW products)


// setup() function -- runs once at startup --------------------------------

void setup() {
  // These lines are specifically to support the Adafruit Trinket 5V 16 MHz.
  // Any other board, you can remove this part (but no harm leaving it):
#if defined(__AVR_ATtiny85__) && (F_CPU == 16000000)
  clock_prescale_set(clock_div_1);
#endif
  // END of Trinket-specific code.

  strip.begin();           // INITIALIZE NeoPixel strip object (REQUIRED)
  strip.show();            // Turn OFF all pixels ASAP
  strip.setBrightness(50); // Set BRIGHTNESS to about 1/5 (max = 255)
}


// loop() function -- runs repeatedly as long as board is on ---------------

void loop() {
  // Fill along the length of the strip in various colors...
  colorWipe(strip.Color(255,   0,   0), 50); // Red
  colorWipe(strip.Color(  0, 255,   0), 50); // Green
  colorWipe(strip.Color(  0,   0, 255), 50); // Blue

  // Do a theater marquee effect in various colors...
  theaterChase(strip.Color(127, 127, 127), 50); // White, half brightness
  theaterChase(strip.Color(127,   0,   0), 50); // Red, half brightness
  theaterChase(strip.Color(  0,   0, 127), 50); // Blue, half brightness

  rainbow(10);             // Flowing rainbow cycle along the whole strip
  theaterChaseRainbow(50); // Rainbow-enhanced theaterChase variant
}


// Some functions of our own for creating animated effects -----------------

// Fill strip pixels one after another with a color. Strip is NOT cleared
// first; anything there will be covered pixel by pixel. Pass in color
// (as a single 'packed' 32-bit value, which you can get by calling
// strip.Color(red, green, blue) as shown in the loop() function above),
// and a delay time (in milliseconds) between pixels.
void colorWipe(uint32_t color, int wait) {
  for(int i=0; i<strip.numPixels(); i++) { // For each pixel in strip...
    strip.setPixelColor(i, color);         //  Set pixel's color (in RAM)
    strip.show();                          //  Update strip to match
    delay(wait);                           //  Pause for a moment
  }
}

// Theater-marquee-style chasing lights. Pass in a color (32-bit value,
// a la strip.Color(r,g,b) as mentioned above), and a delay time (in ms)
// between frames.
void theaterChase(uint32_t color, int wait) {
  for(int a=0; a<10; a++) {  // Repeat 10 times...
    for(int b=0; b<3; b++) { //  'b' counts from 0 to 2...
      strip.clear();         //   Set all pixels in RAM to 0 (off)
      // 'c' counts up from 'b' to end of strip in steps of 3...
      for(int c=b; c<strip.numPixels(); c += 3) {
        strip.setPixelColor(c, color); // Set pixel 'c' to value 'color'
      }
      strip.show(); // Update strip with new contents
      delay(wait);  // Pause for a moment
    }
  }
}

// Rainbow cycle along whole strip. Pass delay time (in ms) between frames.
void rainbow(int wait) {
  // Hue of first pixel runs 5 complete loops through the color wheel.
  // Color wheel has a range of 65536 but it's OK if we roll over, so
  // just count from 0 to 5*65536. Adding 256 to firstPixelHue each time
  // means we'll make 5*65536/256 = 1280 passes through this loop:
  for(long firstPixelHue = 0; firstPixelHue < 5*65536; firstPixelHue += 256) {
    // strip.rainbow() can take a single argument (first pixel hue) or
    // optionally a few extras: number of rainbow repetitions (default 1),
    // saturation and value (brightness) (both 0-255, similar to the
    // ColorHSV() function, default 255), and a true/false flag for whether
    // to apply gamma correction to provide 'truer' colors (default true).
    strip.rainbow(firstPixelHue);
    // Above line is equivalent to:
    // strip.rainbow(firstPixelHue, 1, 255, 255, true);
    strip.show(); // Update strip with new contents
    delay(wait);  // Pause for a moment
  }
}

// Rainbow-enhanced theater marquee. Pass delay time (in ms) between frames.
void theaterChaseRainbow(int wait) {
  int firstPixelHue = 0;     // First pixel starts at red (hue 0)
  for(int a=0; a<30; a++) {  // Repeat 30 times...
    for(int b=0; b<3; b++) { //  'b' counts from 0 to 2...
      strip.clear();         //   Set all pixels in RAM to 0 (off)
      // 'c' counts up from 'b' to end of strip in increments of 3...
      for(int c=b; c<strip.numPixels(); c += 3) {
        // hue of pixel 'c' is offset by an amount to make one full
        // revolution of the color wheel (range 65536) along the length
        // of the strip (strip.numPixels() steps):
        int      hue   = firstPixelHue + c * 65536L / strip.numPixels();
        uint32_t color = strip.gamma32(strip.ColorHSV(hue)); // hue -> RGB
        strip.setPixelColor(c, color); // Set pixel 'c' to value 'color'
      }
      strip.show();                // Update strip with new contents
      delay(wait);                 // Pause for a moment
      firstPixelHue += 65536 / 90; // One cycle of color wheel over 90 frames
    }
  }
}

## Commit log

2025-10-25 Added electronic designs
    [3DESPWrover-B_Cu.gbr, 3DESPWrover-B_Mask.gbr, 3DESPWrover-B_Paste.gbr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]
2026-04-05 Added baseline alg for comparison: Weisfeiler–Lehman (WL) kernel + linear SVM
2026-04-07 Added test neighbors and shape classification results for table 372 with damage
    [testNeighbors_Table_372_Damage1775569816.637865.csv]
2026-04-08 Move testNeighbors_Table_372_Damage CSV to Damaged folder
    [testNeighbors_Table_372_Damage1775569816.637865.csv]
2026-04-09 Added testneighbors damaged boat 144
    [testNeighbors_Boat_144_Damage1775743478.8579018.csv]
2026-04-10 Added new test neighbors to table 372 damage
    [testNeighbors_Table_372_Damage1775810770.9797254.csv]
